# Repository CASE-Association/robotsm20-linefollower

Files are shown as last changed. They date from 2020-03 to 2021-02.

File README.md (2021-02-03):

# Blitz V2
Project repository for the line follower **Blitz V2** to compete in Robot SM 2020. Last years robot was [Blitz V1](https://github.com/caselabbet/robotsm19-linefollower).

Below is a rendered version of **Blitz V2**.
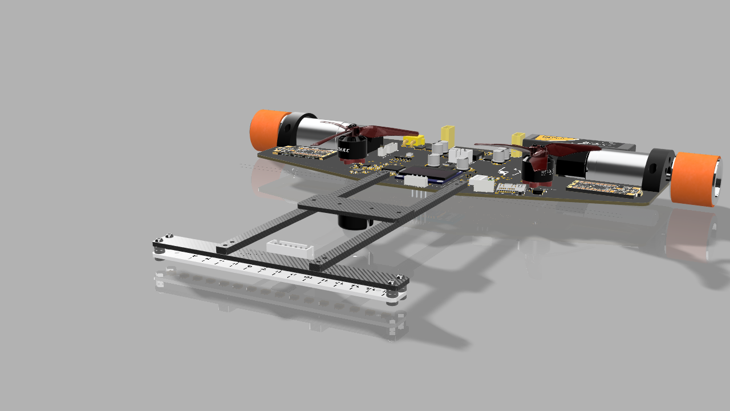
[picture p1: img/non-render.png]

## Goals 
- Utilize more advanced control algorithm.
    - Acceleration control
        - Speed trajectory planner
    - Speed control
        - PID + Anti windup + Active damping
    - Position control
        - PID + Anti windup + Active damping
    - State space model + LQG controller (*optional*)
    - MPC - Model Predictive Conrol (*optional)*
- Map race track + Path planner (*optional*)
- Beat last years result and take 1st place. (*not optional*) 
- Added hardware and improvements
    - Use of suction/exhuast fans
    - Single PCB
    - Bluetooth communication
    - High power motors (11W vs 1/2W)
 
## Directories 
```
robotsm20-linefollower
├── datasheets      
├── hardware        
│   ├── cad         # 3D models
│   │   └── stl     # 3D print files
│   └── pcb         # Schematic, layout and production files
├── img             
├── simulation      # Matlab + simulink simulations
└── software
    ├── Inc         # C header files
    └── Src         # C source files
  ```

## Development enviroment
The microcontroller configuration for peripherals such as ADC, GPIO, TIM, Clock etc. is set up via [STM32CubeMX](https://www.st.com/en/development-tools/stm32cubemx.html) (GUI) and is then ported to a PlatformIO project with the [stm32pio](https://github.com/ussserrr/stm32pio) command. The software is developed in the [VS Code](https://code.visualstudio.com/) IDE with the [PlatformIO](https://platformio.org/) plugin.

This makes it possible to generate base code for initialization of peripherals with the powerful configurator <b>STM32CubeMX</b> but also use the great </b>PlatformIO + VS code</b> ecosystem to manage compiling, uploading, debugging and scripting tasks.

## Installation
In order to update configuration in <b>STM32CubeMX</b> and then update <b>PlatformIO</b> project you need to set up your development enviroment:
 - Create a `boards` directory in your platformio home folder:
    - Unix: `~/.platformio/`
    - Windows: `%HOMEPATH%\.platformio`
 - Copy the custom board `stm32f405rg.json` to the newly created `boards` directory.
 - Verify that the board has been added by running `platformio boards stm32` and find the stm32f405 board.
    <details>
    <summary><b>Common problems</b></summary>

    - If it is not in the list, make sure you put the `boards` in the correct folder and spelled it right.

    - [platformio is not recognized as an internal command](https://docs.platformio.org/en/latest/installation.html#install-shell-commands) 
    </details>
- Rename the file `stm32pio_template.ini` inside the `software` folder to `stm32pio.ini`and fill it out according to the template:
 ```` ini
[app]
java_cmd = java
platformio_cmd = platformio
cubemx_cmd = path/to/cubemx_program

[project]
cubemx_script_content = config load path/to/cubemx_file.ioc
	generate code path/to/projectFolder
	exit
platformio_ini_patch_content = [platformio]
	include_dir = Inc
	src_dir = Src
ioc_file = path/to/cubemxfile.ioc
board = stm32f405rg
````

<details><summary>Unix example</summary>

``` ini
[app]
java_cmd = java
platformio_cmd = platformio
cubemx_cmd = /Applications/STMicroelectronics/STM32CubeMX.app/Contents/Resources/STM32CubeMX

[project]
cubemx_script_content = config load /Users/isakaslund/Documents/code/robotsm20-linefollower/software/software.ioc
	generate code /Users/isakaslund/Documents/code/robotsm20-linefollower/software/
	exit
platformio_ini_patch_content = [platformio]
	include_dir = Inc
	src_dir = Src
ioc_file = /Users/isakaslund/Documents/code/robotsm20-linefollower/software/software.ioc
board = stm32f405rg

```
</details>
<details><summary>Windows example</summary>

``` ini
[app]
java_cmd = java
platformio_cmd = platformio
cubemx_cmd = C:/Program Files/STMicroelectronics/STM32Cube/STM32CubeMX/STM32CubeMX.exe

[project]
cubemx_script_content = config load C:\Users\Isak\Documents\GitHub\robotsm20-linefollower\software\software.ioc
	generate code C:\Users\Isak\Documents\GitHub\robotsm20-linefollower
	exit
platformio_ini_patch_content = [platformio]
	include_dir = Inc
	src_dir = Src
	
ioc_file = C:\Users\Isak\Documents\GitHub\robotsm20-linefollower\software\software.ioc
board = stm32f405rg

```

</details>

Your `software` folder should look this when finished
```
software
├── Inc
│   ├── header_files.h
│   ├── ...
├── Src
│   ├── c_files.c
│   ├── ...
├── platformio.ini
├── software.ioc
├── stm32f405rg.json
└── stm32pio.ini
```

## Usage
#### Configuration change
Change configuration of peripherals in the STM32CubeMX file `software.ioc` and then save project. **DO NOT** click the `generate code` button. 

To then update the `platformio` project run the following command inside the `software` folder:
``` sh
$ stm32pio generate
```

#### Building
Use the platform build task or press the "✓" button in the bottom left in VS code

#### Uploading
A programmer called [ST-Link](https://docs.platformio.org/en/latest/plus/debug-tools/stlink.html) is needed to upload by connecting it to the SWD pins found on the robot.

Use the platform io upload task or press the "⇨" button in the bottom left in vs code. 

#### Debugging
With the STM32 processesor you can do more then `Serial.println()` debugging over serial.
You can step debug, inspect/change variables, set breakpoints and more by using the dedicated debugger/programmer `ST-Link` and the [platformio unified debugger](https://docs.platformio.org/en/latest/plus/debugging.html).

When setup you can start debugging by going to `Debug` -> `Start debugging` in the menu bar. 

## Contributors
  - Isak Åslund - aslundisak@gmail.com
  - Oskar Johansson - oskaj@student.chalmers.se

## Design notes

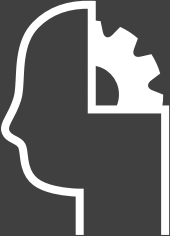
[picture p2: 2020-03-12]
hardware/pcb/decals/case_head.png

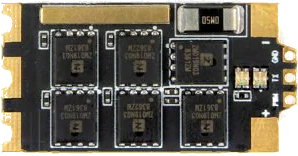
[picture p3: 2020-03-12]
hardware/pcb/decals/ESC_top.png

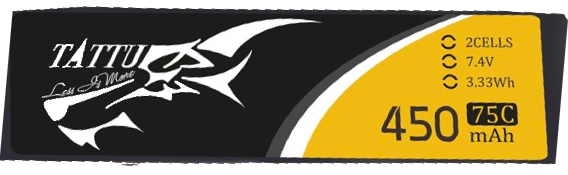
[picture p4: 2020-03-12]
hardware/pcb/decals/Tatt_2s_450mAh.png

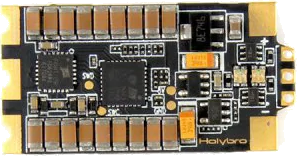
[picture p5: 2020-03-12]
hardware/pcb/decals/ESC_bottom.png

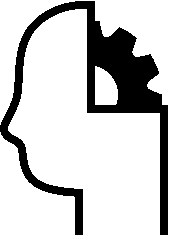
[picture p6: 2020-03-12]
hardware/pcb/case.bmp

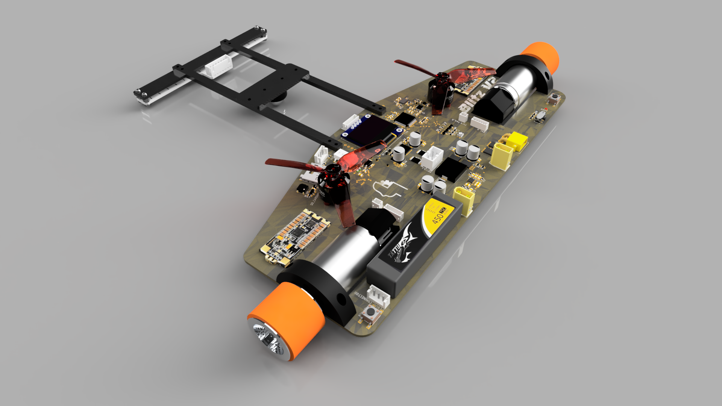
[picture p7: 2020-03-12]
img/side.png

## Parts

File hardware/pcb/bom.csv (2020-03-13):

Qty | Value | Device | Package | Parts | Description | DATASHEET-URL | DESCRIPTION | MANUFACTURER_PART_NUMBER | MOUSER_PART_NUMBER
1 |  | C-EUC0603 | C0603 | C47 | CAPACITOR, European symbol
1 |  | LEDCHIPLED_0603 | CHIPLED_0603 | LED2 | LED
1 |  | MICRO_SD_WE_693071010811 | 6,93071E+11 | SD_CARDHOLDER | WR-CRD Micro SD Card Connector Push & Push 8 pins | https://www.we-online.com/catalog/datasheet/693071010811.pdf |  | 6,93071E+11
8 | 0.1u | C-EUC0603 | C0603 | C31, C32, C34, C35, C37, C39, C40, C46 | CAPACITOR, European symbol
2 | 0.1µF | C-EUC0603 | C0603 | C3, CVCC | CAPACITOR, European symbol
4 | 0.1µF | C-EUC0805 | C0805 | C6, C7, C13, C18 | CAPACITOR, European symbol
1 | 0.68µH | SRP1238A-XXXX | INDM135125X330N | U$3 | Inductor
2 | 0R | R-EU_R0603 | R0603 | R38, R40 | RESISTOR, European symbol
1 | 1.5nF | C-EUC0805 | C0805 | C19 | CAPACITOR, European symbol
1 | 100 | R-EU_R0603 | R0603 | R37 | RESISTOR, European symbol
2 | 100R | R-EU_R0603 | R0603 | R3, R4 | RESISTOR, European symbol
2 | 100nF | C-EUC0603 | C0603 | C42, C43 | CAPACITOR, European symbol
1 | 100nF | C-EUC0805 | C0805 | C21 | CAPACITOR, European symbol
1 | 100pF | C-EUC0805 | C0805 | C26 | CAPACITOR, European symbol
6 | 100uF | WCAP-ASLL-WEWCAP-ASLL | CAPAE660X700N | C4, C15, C24, C25, C29, C30
1 | 105k | R-EU_R0603 | R0603 | R5 | RESISTOR, European symbol
2 | 10R | R-EU_R0603 | R0603 | R14, R15 | RESISTOR, European symbol
23 | 10k | R-EU_R0603 | R0603 | R1, R2, R7, R8, R11, R13, R16, R17, R18, R21, R23, R26, R27, R30, R31, R35, R39, R41, R42, R44, R45, R47, R48 | RESISTOR, European symbol
1 | 110pF | C-EUC0805 | C0805 | C20 | CAPACITOR, European symbol
1 | 120nF | C-EUC0603 | C0603 | C44 | CAPACITOR, European symbol
1 | 15.4k | R-EU_R0603 | R0603 | R10 | RESISTOR, European symbol
1 | 150141M173100 | 150141M173100 | 150141M173100 | LED1 | Wurth Elektronik 150141M173100 Common Anode RGB LED
1 | 19.4k | R-EU_R0603 | R0603 | R22 | RESISTOR, European symbol
1 | 1u | C-EUC0603 | C0603 | C33 | CAPACITOR, European symbol
2 | 2.2u | C-EUC0603 | C0603 | C36, C38 | CAPACITOR, European symbol
2 | 20k | R-EU_R0603 | R0603 | R6, R43 | RESISTOR, European symbol
4 | 22µF | C-EUC0603 | C0603 | C8, C11, C12, C17 | CAPACITOR, European symbol
5 | 22µF | C-EUC0805 | C0805 | C9, C22, C23, C27, C28 | CAPACITOR, European symbol
1 | 270pF | C-EUC0603 | C0603 | COSC | CAPACITOR, European symbol
1 | 3.14k | R-EU_R0603 | R0603 | ROSC | RESISTOR, European symbol
1 | 300R | R-EU_R0603 | R0603 | R32 | RESISTOR, European symbol
1 | 300pF | C-EUC0603 | C0603 | C16 | CAPACITOR, European symbol
1 | 3300pF | C-EUC0805 | C0805 | C10 | CAPACITOR, European symbol
2 | 4.7nF | C-EUC0603 | C0603 | C1, C2 | CAPACITOR, European symbol
1 | 4.7µF | C-EUC0805 | C0805 | C14 | CAPACITOR, European symbol
1 | 50R | R-EU_R0603 | R0603 | R36 | RESISTOR, European symbol
1 | 6.8nF | C-EUC0603 | C0603 | C45 | CAPACITOR, European symbol
1 | 62k | R-EU_R0603 | R0603 | R46 | RESISTOR, European symbol
1 | 75k | R-EU_R0603 | R0603 | R9 | RESISTOR, European symbol
1 | 88k | R-EU_R0603 | R0603 | R12 | RESISTOR, European symbol
1 | BNO055 | BNO055 | BNO055 | IMU-BNO055 | IMUs - Inertial Measurement Units Absolute Orientation 9-Axis Sensor |  | IMUs - Inertial Measurement Units Absolute Orientation 9-Axis Sensor | BNO055 | 262-BNO055
4 | BSS138LT3G | BSS138LT3G | SOT23 | Q5, Q6, Q7, Q8 | BSS138LT3G N-Channel Mosfet (SOT-23)
4 | CSD17301Q5A | CSD17301Q5A | Q5A | U$2, U$8, U$9, U$10 | CSD17301Q5A
1 | CTS_219-4LPST | CTS_219-4LPST | DIPSWITCH_4P_SMD | SW1 | 219-4LPST - Standard 4 position DIP-Switch - SMD
1 | DIODE_1N4148WX | DIODE_1N4148WX | 1N4148WX_SOD-323-2 | U$5
1 | DISPLAY-OLED-128X64-I2C | DISPLAY-OLED-128X64-I2C | DISPLAY-OLED-128X64-I2C | OLED_DISPLAY | OLED 128x63 - I2C - 0.96";";";";";";";";";";";";";";";";";"; 1" | INA2181 | INA2181
1 | JS202011AQN | JS202011AQN | JS202011AQN | BATT_SWITCH | JS202011AQN
2 | JST-EH-03 | EH_B3B-EH | B3B-EH | DEBUG_CONNECTOR, UART_CONNECTOR | JST EH Connector, through hole, 3 pin, top entry
1 | LM1117-3.3 | LM1117-3.3 | SOT230P700X180-4 | LDO_3V3 | LM1117
1 | MCP1501T-XXE | MCP1501T-XXE | SON50P200X200X80-9T80X120N | LDO_VREF_1V8 | MCP1501T-XXE
2 | R001 | R-EU_R2512W | R2512W | MOTOR_LR, MOTOR_RR | RESISTOR, European symbol
1 | R002 | R-EU_R2512W | R2512W | RSENSE | RESISTOR, European symbol
1 | SMT-0540-S-R | SMT-0540-S-R | SMT-0540-S-R | U$1 | Magnetic buzzer
2 | SPLITTER | SPLITTER | SPLITTER | U$4, U$6 | Used for separating grounds
1 | STM32F405RG | STM32F405RG | LQFP-64 | U1 | STM32F405RG Microcontroller
1 | TB67H420FTG | TB67H420FTG | QFN50P700X700X100-49T550N | MOTORDRIVER | TB67H420FTG
2 | TEST-POINT3X5 | TEST-POINT3X5 | PAD.03X.05 | TP_LO1, TP_LO2 | Test Points
4 | TEST_POINTPAD_HOLE | TEST_POINTPAD_HOLE | PAD_HOLE | TP_1V8, TP_3V3, TP_5V, TP_12V
1 | TPS43061RTER | TPS43061RTER | QFN50P300X300X80-17N | BOOST | Low Iq, Synchronous Boost Controller with Wide Input Voltage and 5.5V Gate Drive for Low Qg NexFETs |  | Low Iq, Synchronous Boost Controller with Wide Input Voltage and 5.5V Gate Drive for Low Qg NexFETs | TPS43061RTER | 595-TPS43061RTER
1 | TPS82130SILT | TPS82130SILT | TPS82130SILT | BUCK | 3-A 17V Step-down Converter Module with Integrated Inductor |  | 3-A 17V Step-down Converter Module with Integrated Inductor | TPS82130SILT | 595-TPS82130SILT
2 | TSM2JSMA | TSM2JSMA | TSM2JSMA | BTN_RESET, BTN_SEL | FSM2JSMA Tactile SPST switches
1 | WIRELESS-BLUETOOTH-HC-05 | WIRELESS-BLUETOOTH-HC-05 | WIRELESS-BLUETOOTH-HC-05 | BT_HC05 | Bluetooth Transceiver Module based on HC-05 board
2 | XH-02 | XH-02 | JST-XH-02 | MOTOR_L, MOTOR_R | JST EX Connector, through hole, 2 pin, top entry
2 | XT30 | XT30 | XT30 | FAN_POWER_L, FAN_POWER_R | XT60 Connector
1 | XT30PW-M | XT30PW-M | XT30PW-M | U$15
2 | ZH | ZR_B2B-ZR | B2B-ZR | PWM_FAN_L, PWM_FAN_R | JST ZR Connector, through hole, 2 pin, top entry
1 | ZH | ZR_B7B-ZR | B7B-ZR | XLINE | JST ZR Connector, through hole, 7 pin, top entry
2 | ZH-6 | ZR_B6B-ZR | B6B-ZR | ENC_L, ENC_R | JST ZR Connector, through hole, 6 pin, top entry

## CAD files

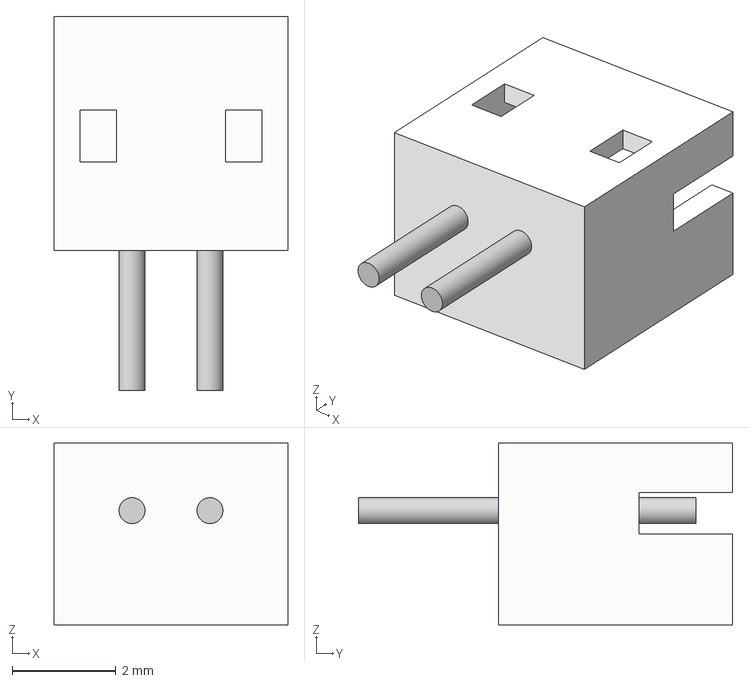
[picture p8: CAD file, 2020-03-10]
hardware/pcb/step/JST-ZH-02.step
4.50 x 7.20 x 3.50 mm

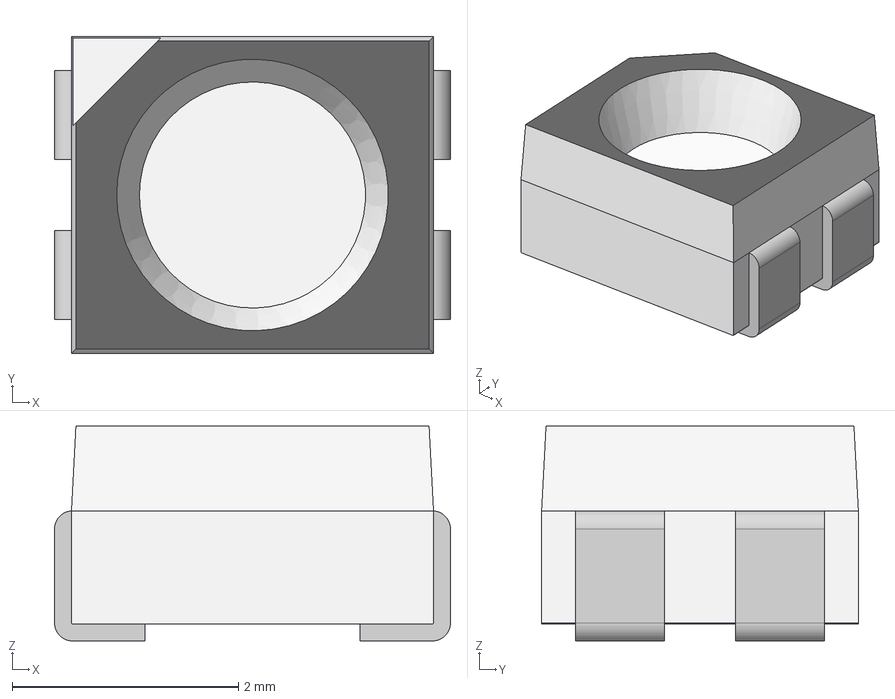
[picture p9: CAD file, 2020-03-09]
hardware/pcb/step/RGB-LED_15014M173100.step
3.50 x 2.80 x 1.90 mm
base x 2
base (1) x 2
cover
housing

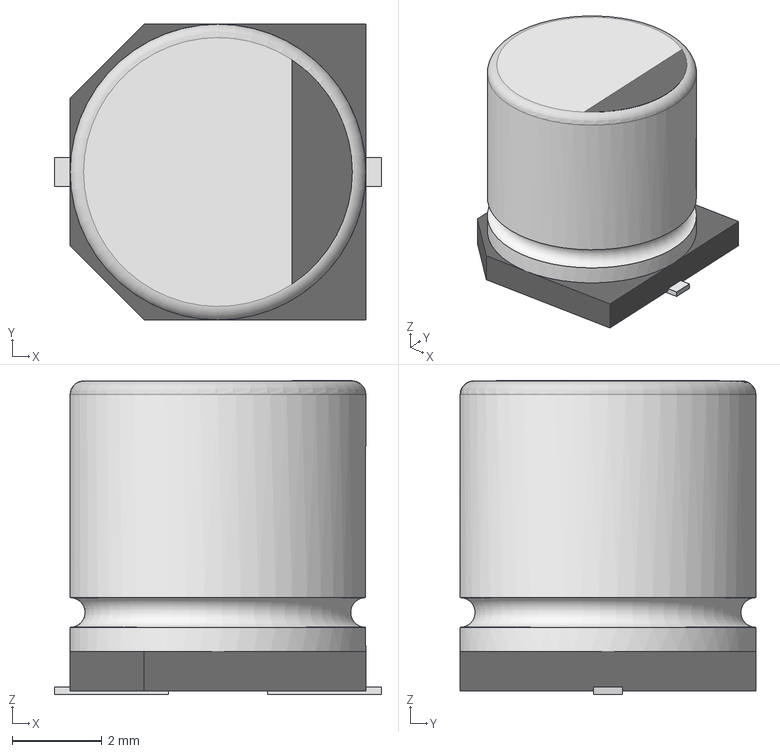
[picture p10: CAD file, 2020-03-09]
hardware/pcb/step/WCAP-ASLL.step
7.30 x 6.60 x 7.01 mm

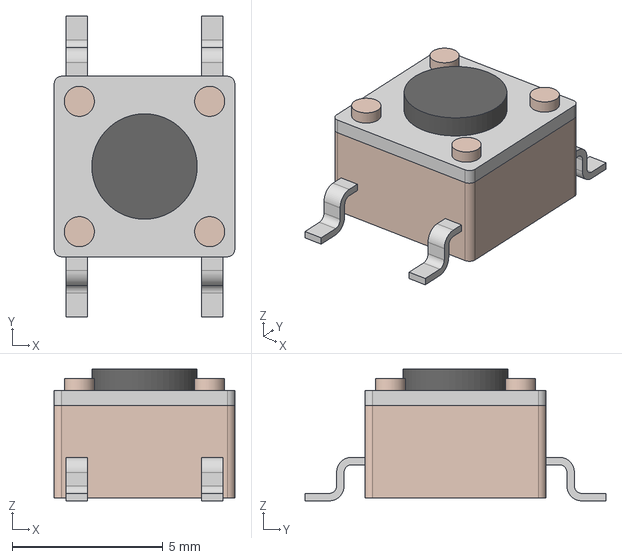
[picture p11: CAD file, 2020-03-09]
hardware/pcb/step/FSM2JSMA.step
6.00 x 10.0 x 4.38 mm

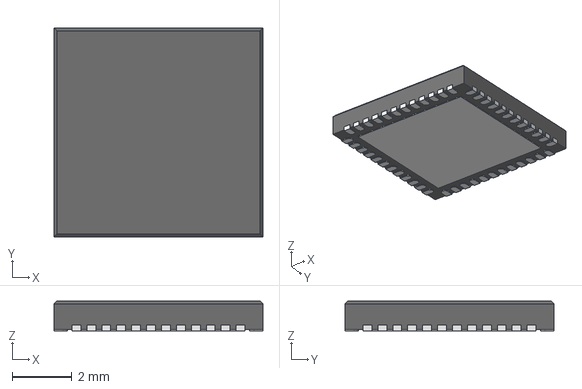
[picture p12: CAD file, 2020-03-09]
hardware/pcb/step/TB67H420_QFN48.step
7.00 x 7.00 x 1.00 mm

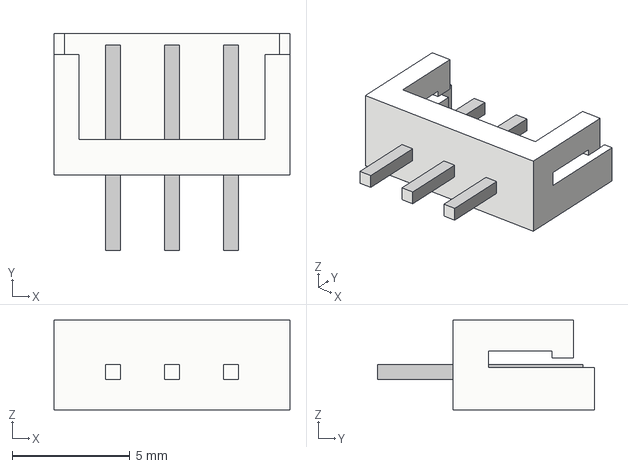
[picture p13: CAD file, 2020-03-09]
hardware/pcb/step/JST-EH-03.step
10.0 x 9.20 x 3.80 mm

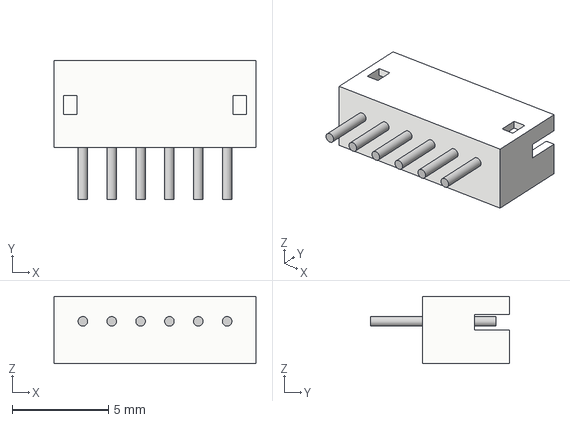
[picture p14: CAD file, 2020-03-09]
hardware/pcb/step/JST-ZH-06.step
10.5 x 7.20 x 3.50 mm

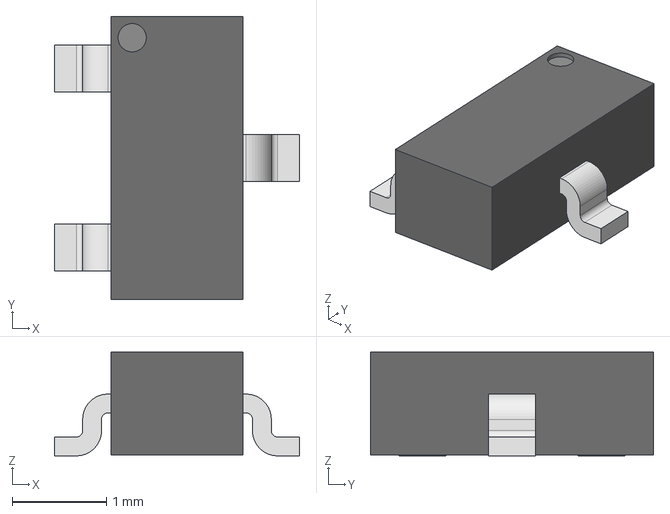
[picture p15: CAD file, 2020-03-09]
hardware/pcb/step/BSS138L.step
2.60 x 3.00 x 1.10 mm

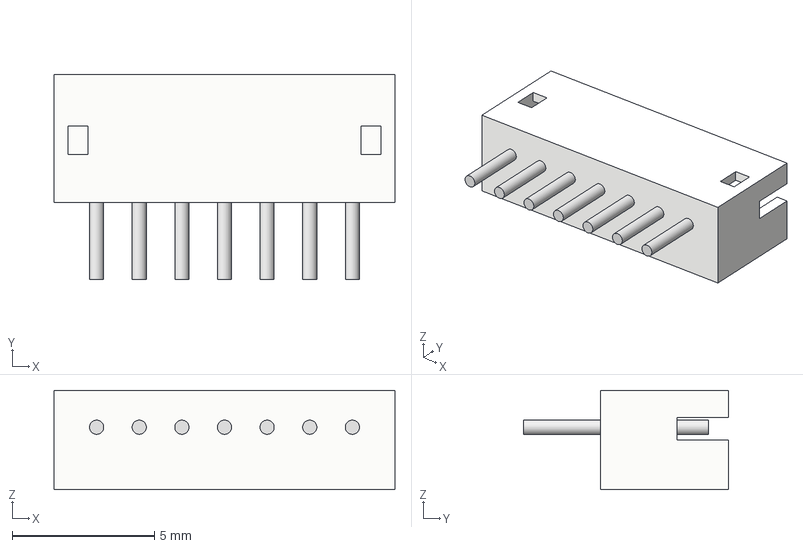
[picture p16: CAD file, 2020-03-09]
hardware/pcb/step/JST-ZH-07.step
12.0 x 7.20 x 3.50 mm

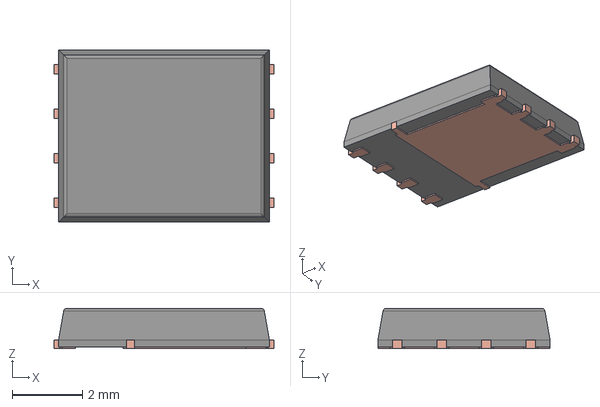
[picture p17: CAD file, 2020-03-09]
hardware/pcb/step/DQJ0008A.stp
6.26 x 4.90 x 1.15 mm
FRAME
MOLD

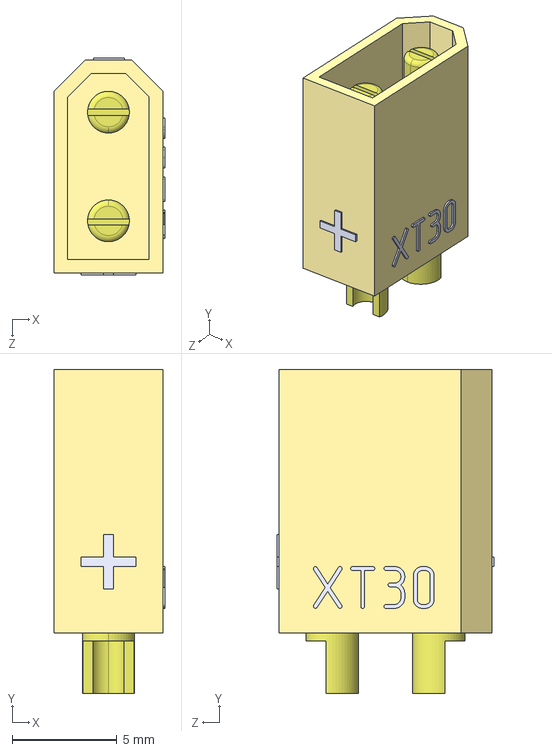
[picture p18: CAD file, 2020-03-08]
hardware/pcb/step/XT30-M.step
5.30 x 15.5 x 10.4 mm

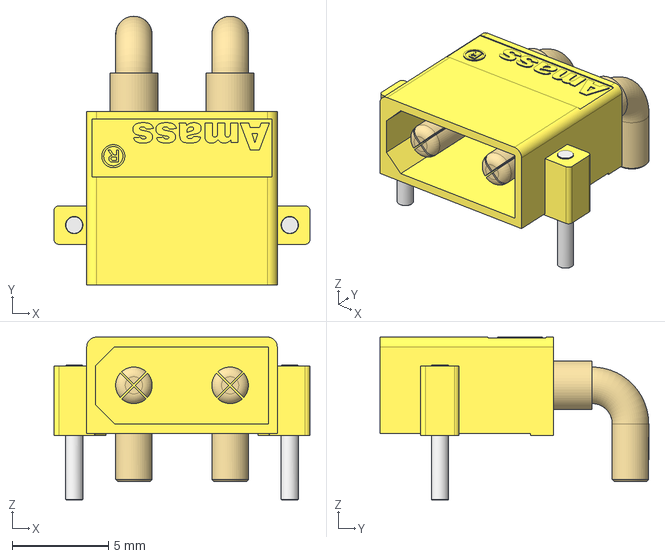
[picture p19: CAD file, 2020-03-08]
hardware/pcb/step/Amass_XT30PW-M_pcb solder.stp
13.3 x 13.9 x 8.45 mm

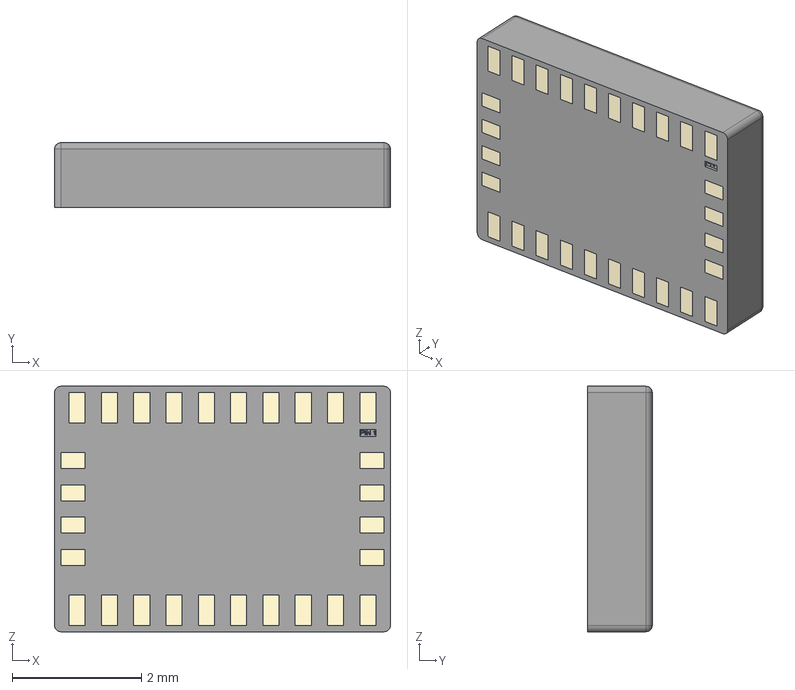
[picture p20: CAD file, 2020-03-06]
hardware/pcb/step/BNO055.step
5.20 x 1.00 x 3.80 mm

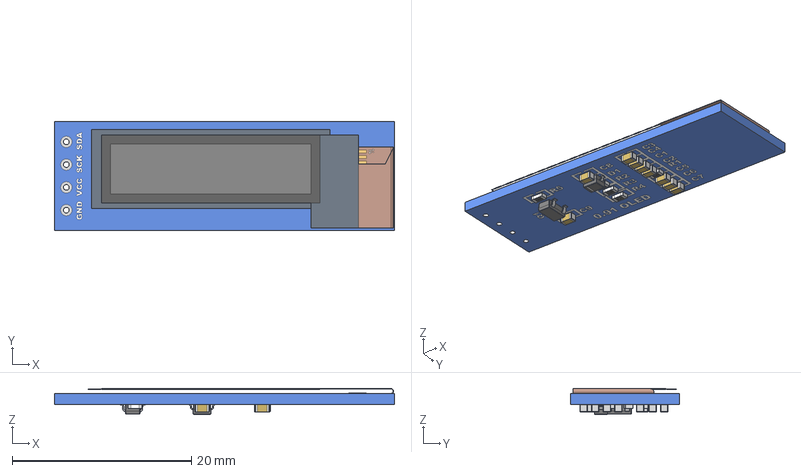
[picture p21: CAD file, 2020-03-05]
hardware/pcb/step/128x32 Oled i2c.stp
37.9 x 12.1 x 2.93 mm
0.91in oled Module - Board
0.91in OLED - Folded Flush - Without Glass
0603 Capacitor x 9
0603 Resistor x 5
SOT23-3
Diode (SOD-323)

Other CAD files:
hardware/pcb/step/JS202011AQN.step
hardware/pcb/step/TPS82130.step
hardware/pcb/step/TPS43061.step

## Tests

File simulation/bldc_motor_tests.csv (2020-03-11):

 | RS1306 + 3blade(black) |  |  | RS1306 + 3blade(red-translucent)
RPM | I | Thrust | RPM | I | Thrust
n/a | n/a | n/a | 8300 | 0,6 | 18,5
Props did not work well when reversed due to extreme shape |  |  | 14000 | 1,8 | 47,8
 |  |  | 18500 | 3,75 | 90
 |  |  | 23000 | 6,5 | 130
 | RS1606 + 3"3B(red-solid) |  |  | RS1606 + 3"4B(black-solid) |  |  | RS1606 + 4"3B(red-solid)
RPM | I | Thrust | RPM | I | Thrust | RPM | I | Thrust
8000 | 0,8 | 6 | 8800 | 1,1 | 18 | 5000 | 0,7 | 16
14000 | 1,9 | 30 | 17000 | 4 | 75 | 7700 | 1,7 | 37
20000 | 3,5 | 70 | 22000 | 7,6 | 124 | 10000 | 3,3 | 68
23000 | 4,5 | 92 |  |  |  | 12000 | 5,3 | 94
24500 | 5 | 110 |  |  |  | 13300 | 7,3 | 115
 | RS2205 + 4"4B(red-solid)
RPM | I | Thrust
5000 | 0,9 | 32
8500 | 2,8 | 90
10000 | 4,35 | 150
11300 | 6,2 | 220
12300 | 7,5 | 275

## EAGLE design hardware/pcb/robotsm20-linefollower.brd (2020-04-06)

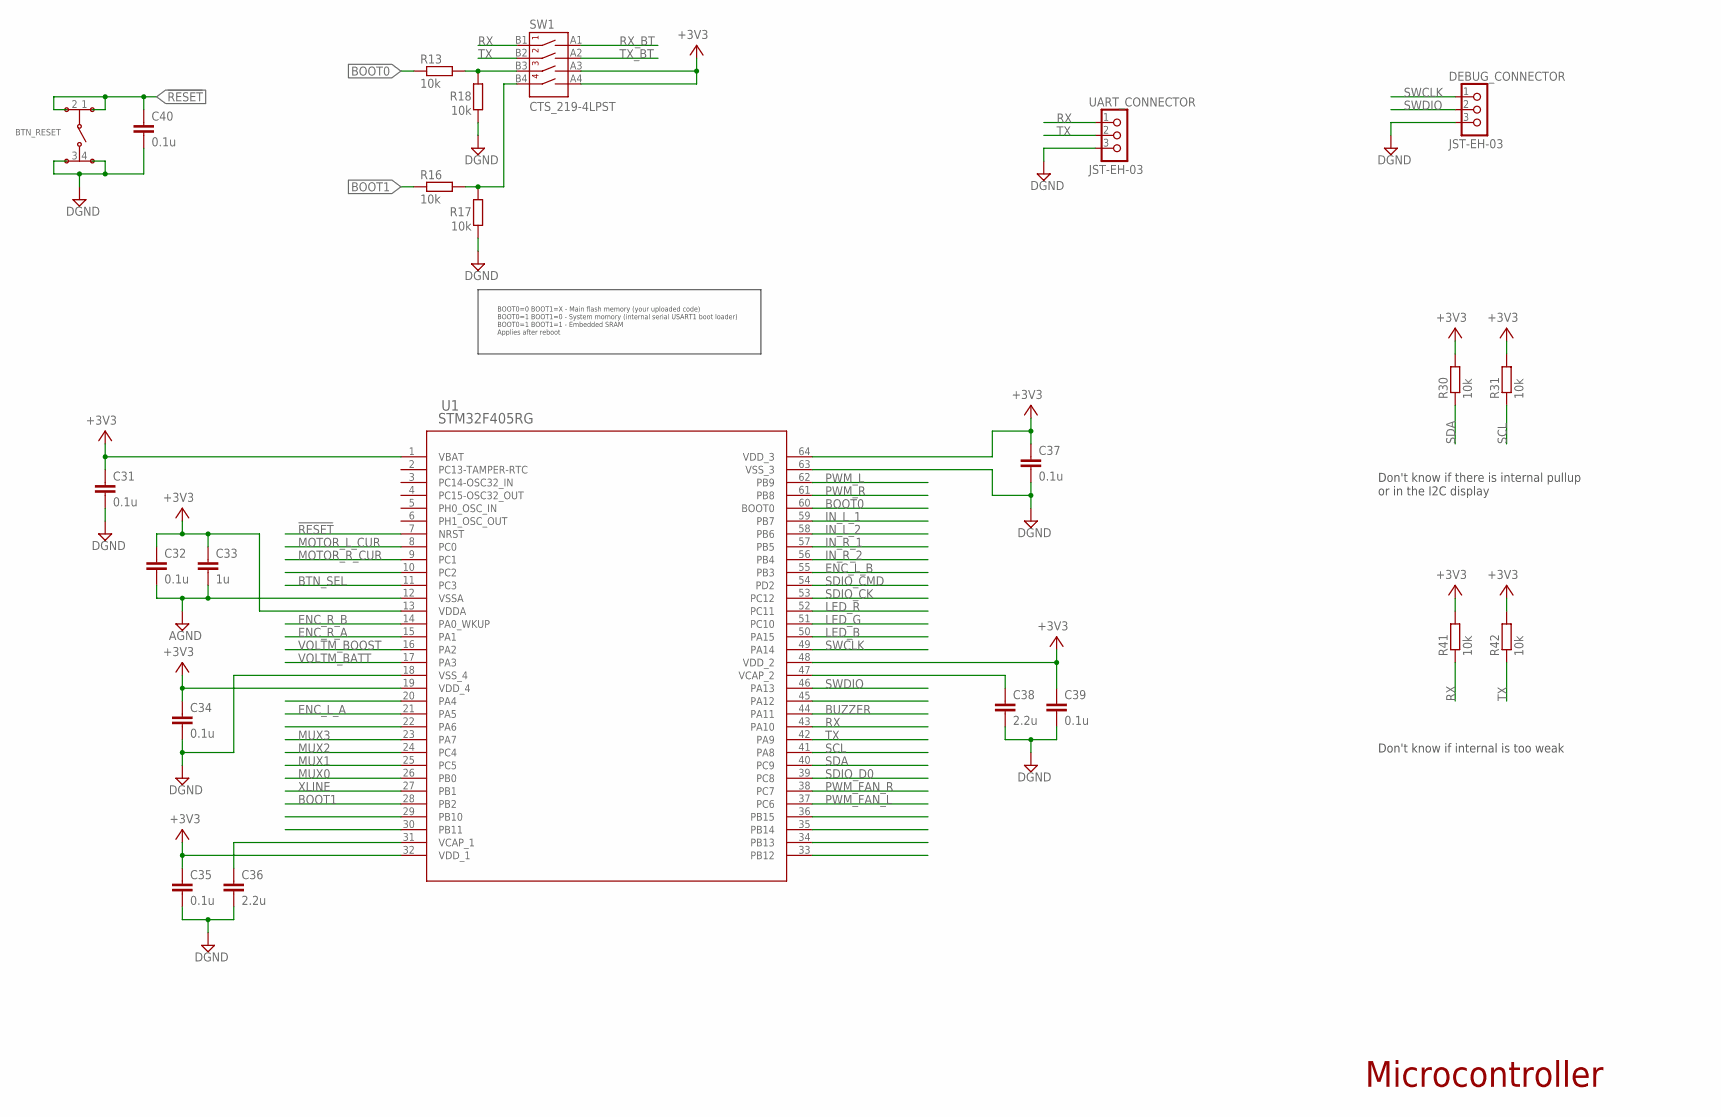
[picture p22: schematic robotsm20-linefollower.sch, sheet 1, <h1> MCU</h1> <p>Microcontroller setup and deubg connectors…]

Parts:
BTN_RESET: TSM2JSMA
C31, C32, C34, C35, C37, C39, C40: 0.1u; C0603
C33: 1u; C0603
C36, C38: 2.2u; C0603
DEBUG_CONNECTOR: JST-EH-03; B3B-EH
R13, R16, R17, R18, R30, R31, R41, R42: 10k; R0603
SW1: CTS_219-4LPST; DIPSWITCH_4P_SMD
U1: STM32F405RG; LQFP-64
UART_CONNECTOR: JST-EH-03; B3B-EH

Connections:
!RESET: BTN_RESET.1, BTN_RESET.2, C40.1, U1.7 (NRST)
+3V3: C31.1, C32.1, C33.1, C34.1, C35.1, C37.1, C39.1, R30.1, R31.1, R41.1, R42.1, SW1.A3, SW1.A4, U1.1 (VBAT), U1.13 (VDDA), U1.19 (VDD_4), U1.32 (VDD_1), U1.48 (VDD_2), U1.64 (VDD_3); also elsewhere on the board
AGND: C32.2, C33.2, U1.12 (VSSA); also elsewhere on the board
BOOT0: R13.2, U1.60 (BOOT0)
BOOT1: R16.1, U1.28 (PB2)
BTN_SEL: U1.11 (PC3); also elsewhere on the board
BUZZER: U1.44 (PA11); also elsewhere on the board
DGND: BTN_RESET.3, BTN_RESET.4, C31.2, C34.2, C35.2, C36.2, C37.2, C38.2, C39.2, C40.2, DEBUG_CONNECTOR.3, R17.1, R18.1, U1.18 (VSS_4), U1.63 (VSS_3), UART_CONNECTOR.3; also elsewhere on the board
ENC_L_A: U1.21 (PA5); also elsewhere on the board
ENC_L_B: U1.55 (PB3); also elsewhere on the board
ENC_R_A: U1.15 (PA1); also elsewhere on the board
ENC_R_B: U1.14 (PA0_WKUP); also elsewhere on the board
IN_L_1: U1.59 (PB7); also elsewhere on the board
IN_L_2: U1.58 (PB6); also elsewhere on the board
IN_R_1: U1.57 (PB5); also elsewhere on the board
IN_R_2: U1.56 (PB4); also elsewhere on the board
LED_B: U1.50 (PA15); also elsewhere on the board
LED_G: U1.51 (PC10); also elsewhere on the board
LED_R: U1.52 (PC11); also elsewhere on the board
MOTOR_L_CUR: U1.8 (PC0); also elsewhere on the board
MOTOR_R_CUR: U1.9 (PC1); also elsewhere on the board
MUX0: U1.26 (PB0); also elsewhere on the board
MUX1: U1.25 (PC5); also elsewhere on the board
MUX2: U1.24 (PC4); also elsewhere on the board
MUX3: U1.23 (PA7); also elsewhere on the board
unnamed: R16.2, R17.2, SW1.B4
unnamed: R13.1, R18.2, SW1.B3
unnamed: C36.1, U1.31 (VCAP_1)
unnamed: C38.1, U1.47 (VCAP_2)
PWM_FAN_L: U1.37 (PC6); also elsewhere on the board
PWM_FAN_R: U1.38 (PC7); also elsewhere on the board
PWM_L: U1.62 (PB9); also elsewhere on the board
PWM_R: U1.61 (PB8); also elsewhere on the board
RX: R41.2, SW1.B1, U1.43 (PA10), UART_CONNECTOR.1
RX_BT: SW1.A1; also elsewhere on the board
SCL: R31.2, U1.41 (PA8); also elsewhere on the board
SDA: R30.2, U1.40 (PC9); also elsewhere on the board
SDIO_CK: U1.53 (PC12); also elsewhere on the board
SDIO_CMD: U1.54 (PD2); also elsewhere on the board
SDIO_D0: U1.39 (PC8); also elsewhere on the board
SWCLK: DEBUG_CONNECTOR.1, U1.49 (PA14)
SWDIO: DEBUG_CONNECTOR.2, U1.46 (PA13)
TX: R42.2, SW1.B2, U1.42 (PA9), UART_CONNECTOR.2
TX_BT: SW1.A2; also elsewhere on the board
VOLTM_BATT: U1.17 (PA3); also elsewhere on the board
VOLTM_BOOST: U1.16 (PA2); also elsewhere on the board
XLINE: U1.27 (PB1); also elsewhere on the board

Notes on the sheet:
Microcontroller
BOOT0=0 BOOT1=X - Main flash memory (your uploaded code) BOOT0=1 BOOT1=0 - System momory (internal serial USART1 boot loader) BOOT0=1 BOOT1=1 - Embedded SRAM Applies after reboot
Don't know if there is internal pullup or in the I2C display
Don't know if internal is too weak

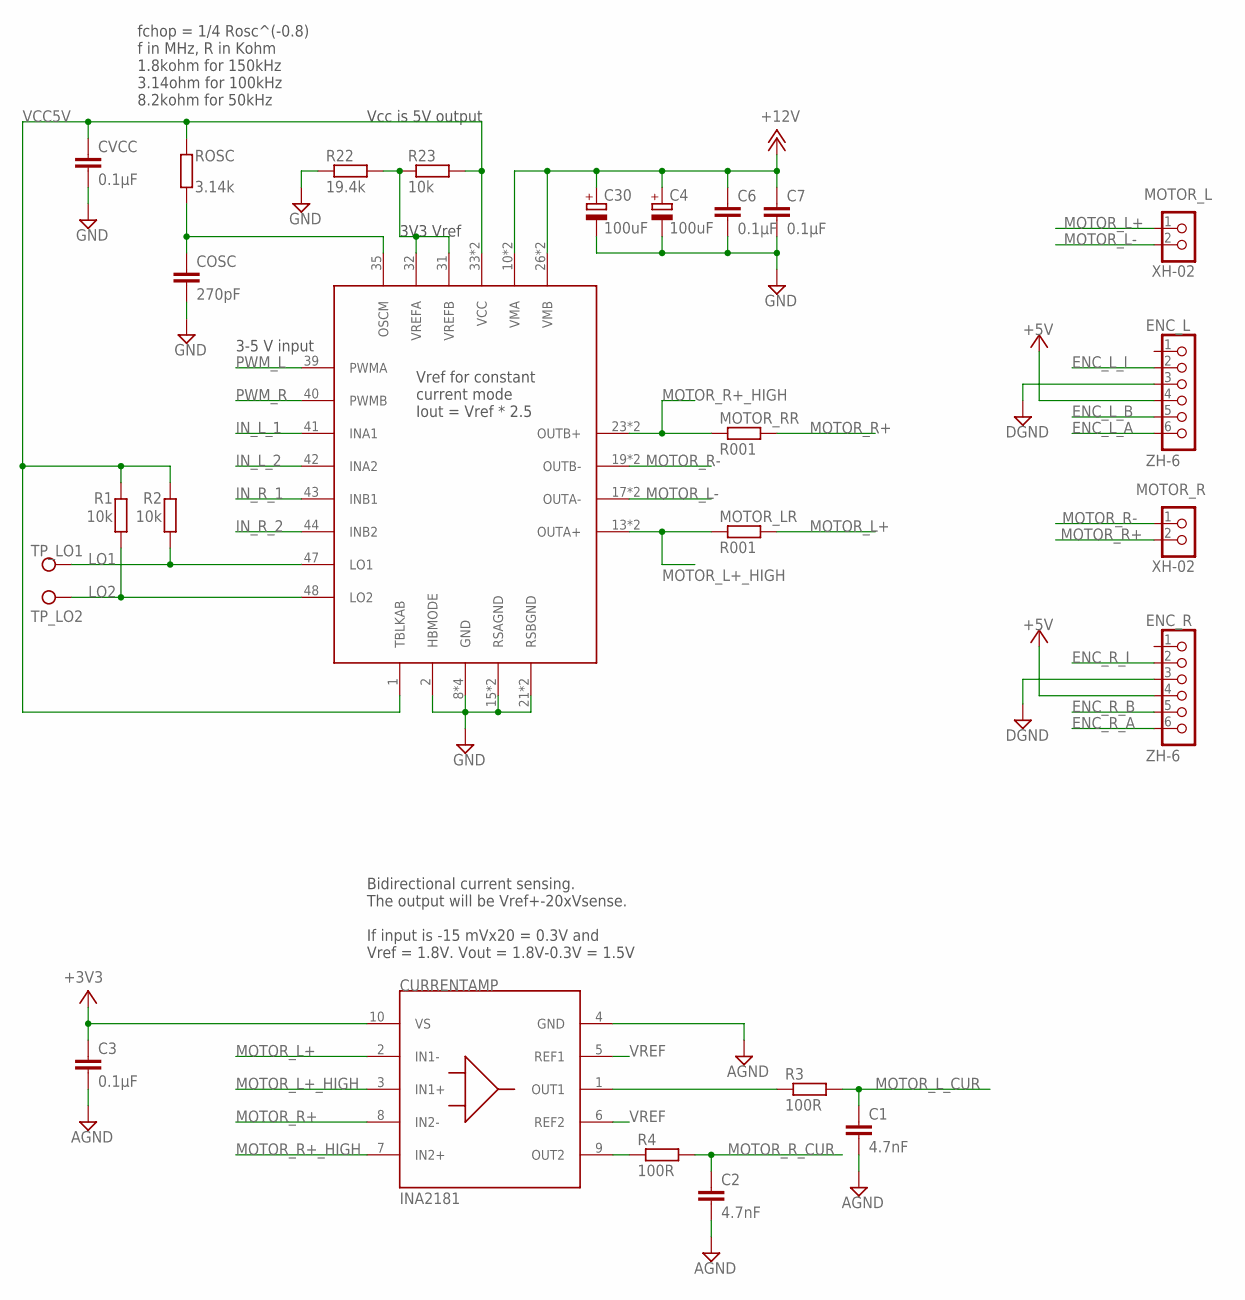
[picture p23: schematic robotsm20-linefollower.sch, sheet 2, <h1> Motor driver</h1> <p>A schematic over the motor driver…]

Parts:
C1, C2: 4.7nF; C0603
C3: 0.1µF; C0603
C4, C30: 100uF; CAPAE660X700N
C6, C7: 0.1µF; C0805
COSC: 270pF; C0603
CURRENTAMP: INA2181; SOP50P490X110-10N
CVCC: 0.1µF; C0603
ENC_L: ZH-6; B6B-ZR
ENC_R: ZH-6; B6B-ZR
MOTORDRIVER: TB67H420FTG; QFN50P700X700X100-49T550N
MOTOR_L: XH-02; JST-XH-02
MOTOR_LR: R001; R2512W
MOTOR_R: XH-02; JST-XH-02
MOTOR_RR: R001; R2512W
R1, R2, R23: 10k; R0603
R3, R4: 100R; R0603
R22: 19.4k; R0603
ROSC: 3.14k; R0603
TP_LO1, TP_LO2: TEST-POINT3X5; PAD.03X.05

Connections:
+3V3: C3.1, CURRENTAMP.10 (VS); also elsewhere on the board
+5V: ENC_L.4, ENC_R.4; also elsewhere on the board
+12V: C4.1 (+), C6.1, C7.1, C30.1 (+), MOTORDRIVER.10 (VMA), MOTORDRIVER.11 (VMA), MOTORDRIVER.26 (VMB), MOTORDRIVER.27 (VMB); also elsewhere on the board
AGND: C1.2, C2.2, C3.2, CURRENTAMP.4 (GND); also elsewhere on the board
DGND: ENC_L.3, ENC_R.3; also elsewhere on the board
ENC_L_A: ENC_L.6; also elsewhere on the board
ENC_L_B: ENC_L.5; also elsewhere on the board
ENC_L_I: ENC_L.2
ENC_R_A: ENC_R.6; also elsewhere on the board
ENC_R_B: ENC_R.5; also elsewhere on the board
ENC_R_I: ENC_R.2
GND: C4.2 (-), C6.2, C7.2, C30.2 (-), COSC.2, CVCC.2, MOTORDRIVER.2 (HBMODE), MOTORDRIVER.8 (GND), MOTORDRIVER.15 (RSAGND), MOTORDRIVER.16 (RSAGND), MOTORDRIVER.21 (RSBGND), MOTORDRIVER.22 (RSBGND), MOTORDRIVER.29 (GND), MOTORDRIVER.30 (GND), MOTORDRIVER.49 (GND), R22.1; also elsewhere on the board
IN_L_1: MOTORDRIVER.41 (INA1); also elsewhere on the board
IN_L_2: MOTORDRIVER.42 (INA2); also elsewhere on the board
IN_R_1: MOTORDRIVER.43 (INB1); also elsewhere on the board
IN_R_2: MOTORDRIVER.44 (INB2); also elsewhere on the board
LO1: MOTORDRIVER.47 (LO1), R2.1, TP_LO1.P$1
LO2: MOTORDRIVER.48 (LO2), R1.1, TP_LO2.P$1
MOTOR_L+: CURRENTAMP.2 (IN1-), MOTOR_L.1, MOTOR_LR.2
MOTOR_L+_HIGH: CURRENTAMP.3 (IN1+), MOTORDRIVER.13 (OUTA+), MOTORDRIVER.14 (OUTA+), MOTOR_LR.1
MOTOR_L-: MOTORDRIVER.17 (OUTA-), MOTORDRIVER.18 (OUTA-), MOTOR_L.2
MOTOR_L_CUR: C1.1, R3.2; also elsewhere on the board
MOTOR_R+: CURRENTAMP.8 (IN2-), MOTOR_R.2, MOTOR_RR.2
MOTOR_R+_HIGH: CURRENTAMP.7 (IN2+), MOTORDRIVER.23 (OUTB+), MOTORDRIVER.24 (OUTB+), MOTOR_RR.1
MOTOR_R-: MOTORDRIVER.19 (OUTB-), MOTORDRIVER.20 (OUTB-), MOTOR_R.1
MOTOR_R_CUR: C2.1, R4.2; also elsewhere on the board
unnamed: CURRENTAMP.9 (OUT2), R4.1
unnamed: CURRENTAMP.1 (OUT1), R3.1
unnamed: MOTORDRIVER.31 (VREFB), MOTORDRIVER.32 (VREFA), R22.2, R23.1
unnamed: COSC.1, MOTORDRIVER.35 (OSCM), ROSC.1
PWM_L: MOTORDRIVER.39 (PWMA); also elsewhere on the board
PWM_R: MOTORDRIVER.40 (PWMB); also elsewhere on the board
VCC5V: CVCC.1, MOTORDRIVER.1 (TBLKAB), MOTORDRIVER.33 (VCC), MOTORDRIVER.34 (VCC), R1.2, R2.2, R23.2, ROSC.2
VREF: CURRENTAMP.5 (REF1), CURRENTAMP.6 (REF2); also elsewhere on the board

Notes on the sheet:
Bidirectional current sensing. The output will be Vref+-20xVsense. If input is -15 mVx20 = 0.3V and Vref = 1.8V. Vout = 1.8V-0.3V = 1.5V
3-5 V input
Vcc is 5V output
3V3 Vref
fchop = 1/4 Rosc^(-0.8) f in MHz, R in Kohm 1.8kohm for 150kHz 3.14ohm for 100kHz 8.2kohm for 50kHz
Vref for constant current mode Iout = Vref * 2.5

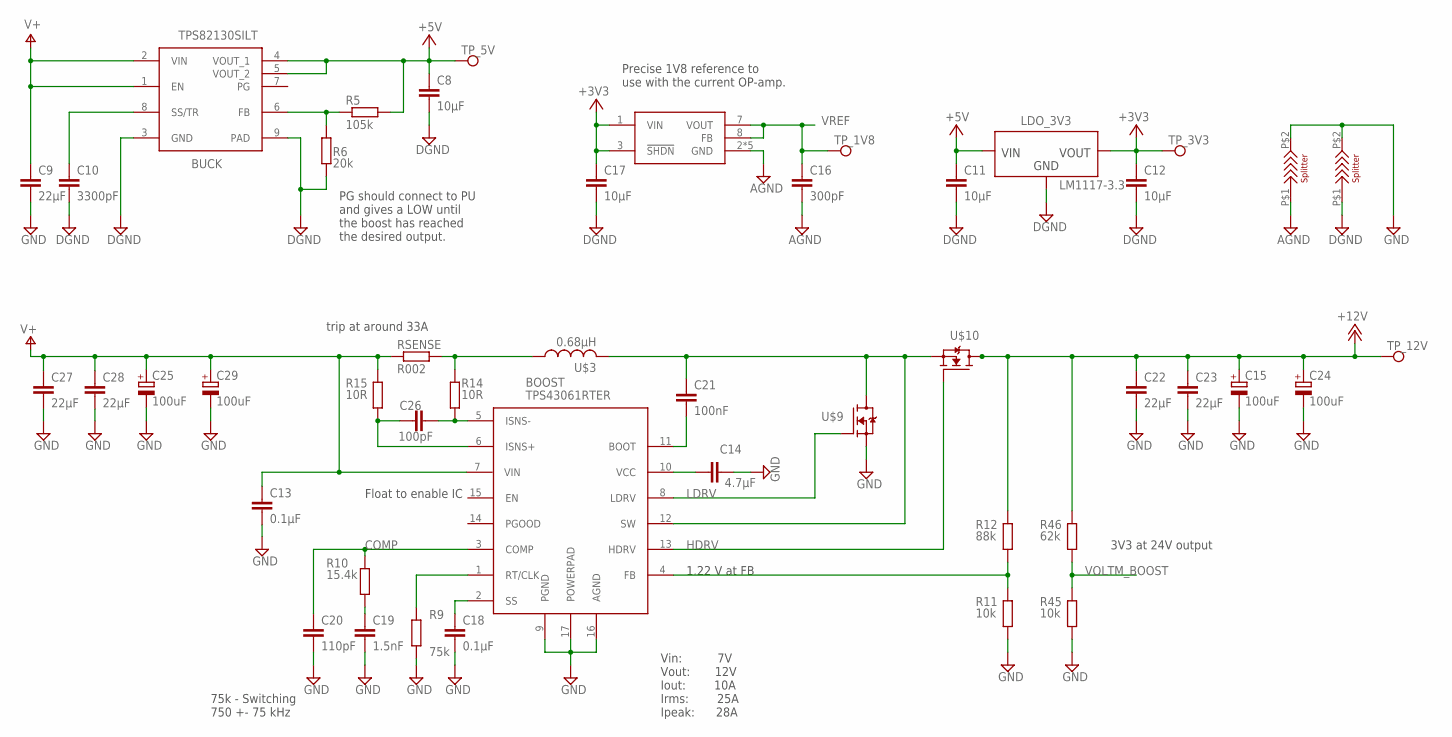
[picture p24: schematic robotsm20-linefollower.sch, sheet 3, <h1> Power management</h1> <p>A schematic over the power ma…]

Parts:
BOOST: TPS43061RTER; QFN50P300X300X80-17N
BUCK: TPS82130SILT
C8, C11, C12, C17: 10µF; C0603
C9, C22, C23, C27, C28: 22µF; C0805
C10: 3300pF; C0805
C13, C18: 0.1µF; C0805
C14: 4.7µF; C0805
C15, C24, C25, C29: 100uF; CAPAE660X700N
C16: 300pF; C0603
C19: 1.5nF; C0805
C20: 110pF; C0805
C21: 100nF; C0805
C26: 100pF; C0805
LDO_3V3: LM1117-3.3; SOT230P700X180-4
LDO_VREF_1V8: MCP1501T-XXE; SON50P200X200X80-9T80X120N
R5: 105k; R0603
R6: 20k; R0603
R9: 75k; R0603
R10: 15.4k; R0603
R11, R45: 10k; R0603
R12: 88k; R0603
R14, R15: 10R; R0603
R46: 62k; R0603
RSENSE: R002; R2512W
TP_1V8, TP_3V3, TP_5V, TP_12V: TEST_POINTPAD_HOLE; PAD_HOLE
U$3: 0.68µH; INDM135125X330N
U$4, U$6: SPLITTER
U$9, U$10: CSD17301Q5A; Q5A

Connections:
+3V3: C12.1, C17.1, LDO_3V3.2 (VOUT), LDO_3V3.4 (VOUT), LDO_VREF_1V8.1 (VIN), LDO_VREF_1V8.3 (!SHDN!), TP_3V3.P$1; also elsewhere on the board
+5V: BUCK.4 (VOUT_1), BUCK.5 (VOUT_2), C8.1, C11.1, LDO_3V3.3 (VIN), R5.2, TP_5V.P$1; also elsewhere on the board
+12V: C15.1 (+), C22.1, C23.1, C24.1 (+), R12.2, R46.2, TP_12V.P$1, U$10.5 (D), U$10.6 (D), U$10.7 (D), U$10.8 (D), U$10.9 (D); also elsewhere on the board
AGND: C16.2, LDO_VREF_1V8.2 (GND), LDO_VREF_1V8.4 (GND), LDO_VREF_1V8.5 (GND), LDO_VREF_1V8.6 (GND), LDO_VREF_1V8.9 (GND), U$4.P$1 (1); also elsewhere on the board
COMP: BOOST.3 (COMP), C20.1, R10.2
DGND: BUCK.3 (GND), BUCK.9 (PAD), C8.2, C10.2, C11.2, C12.2, C17.2, LDO_3V3.1 (GND), R6.1, U$6.P$1 (1); also elsewhere on the board
GND: BOOST.9 (PGND), BOOST.16 (AGND), BOOST.17 (POWERPAD), C9.2, C13.2, C14.2, C15.2 (-), C18.2, C19.2, C20.2, C22.2, C23.2, C24.2 (-), C25.2 (-), C27.2, C28.2, C29.2 (-), R9.1, R11.1, R45.1, U$4.P$2 (2), U$6.P$2 (2), U$9.1 (S), U$9.2 (S), U$9.3 (S); also elsewhere on the board
HDRV: BOOST.13 (HDRV), U$10.4 (G)
LDRV: BOOST.8 (LDRV), U$9.4 (G)
unnamed: BOOST.10 (VCC), C14.1
unnamed: BUCK.8 (SS/TR), C10.1
unnamed: BUCK.6 (FB), R5.1, R6.2
unnamed: BOOST.1 (RT/CLK), R9.2
unnamed: BOOST.2 (SS), C18.1
unnamed: C19.1, R10.1
unnamed: BOOST.11 (BOOT), C21.2
unnamed: R14.2, RSENSE.2, U$3.1
unnamed: BOOST.12 (SW), C21.1, U$3.2, U$9.5 (D), U$9.6 (D), U$9.7 (D), U$9.8 (D), U$9.9 (D), U$10.1 (S), U$10.2 (S), U$10.3 (S)
unnamed: BOOST.4 (FB), R11.2, R12.1
unnamed: BOOST.5 (ISNS-), C26.2, R14.1
unnamed: BOOST.6 (ISNS+), C26.1, R15.1
V+: BOOST.7 (VIN), BUCK.1 (EN), BUCK.2 (VIN), C9.1, C13.1, C25.1 (+), C27.1, C28.1, C29.1 (+), R15.2, RSENSE.1; also elsewhere on the board
VOLTM_BOOST: R45.2, R46.1; also elsewhere on the board
VREF: C16.1, LDO_VREF_1V8.7 (VOUT), LDO_VREF_1V8.8 (FB), TP_1V8.P$1; also elsewhere on the board

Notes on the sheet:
PG should connect to PU and gives a LOW until the boost has reached the desired output.
Precise 1V8 reference to use with the current OP-amp.
75k - Switching 750 +- 75 kHz
1.22 V at FB
trip at around 33A
Vin: 7V Vout: 12V Iout: 10A Irms: 25A Ipeak: 28A
3V3 at 24V output
Float to enable IC

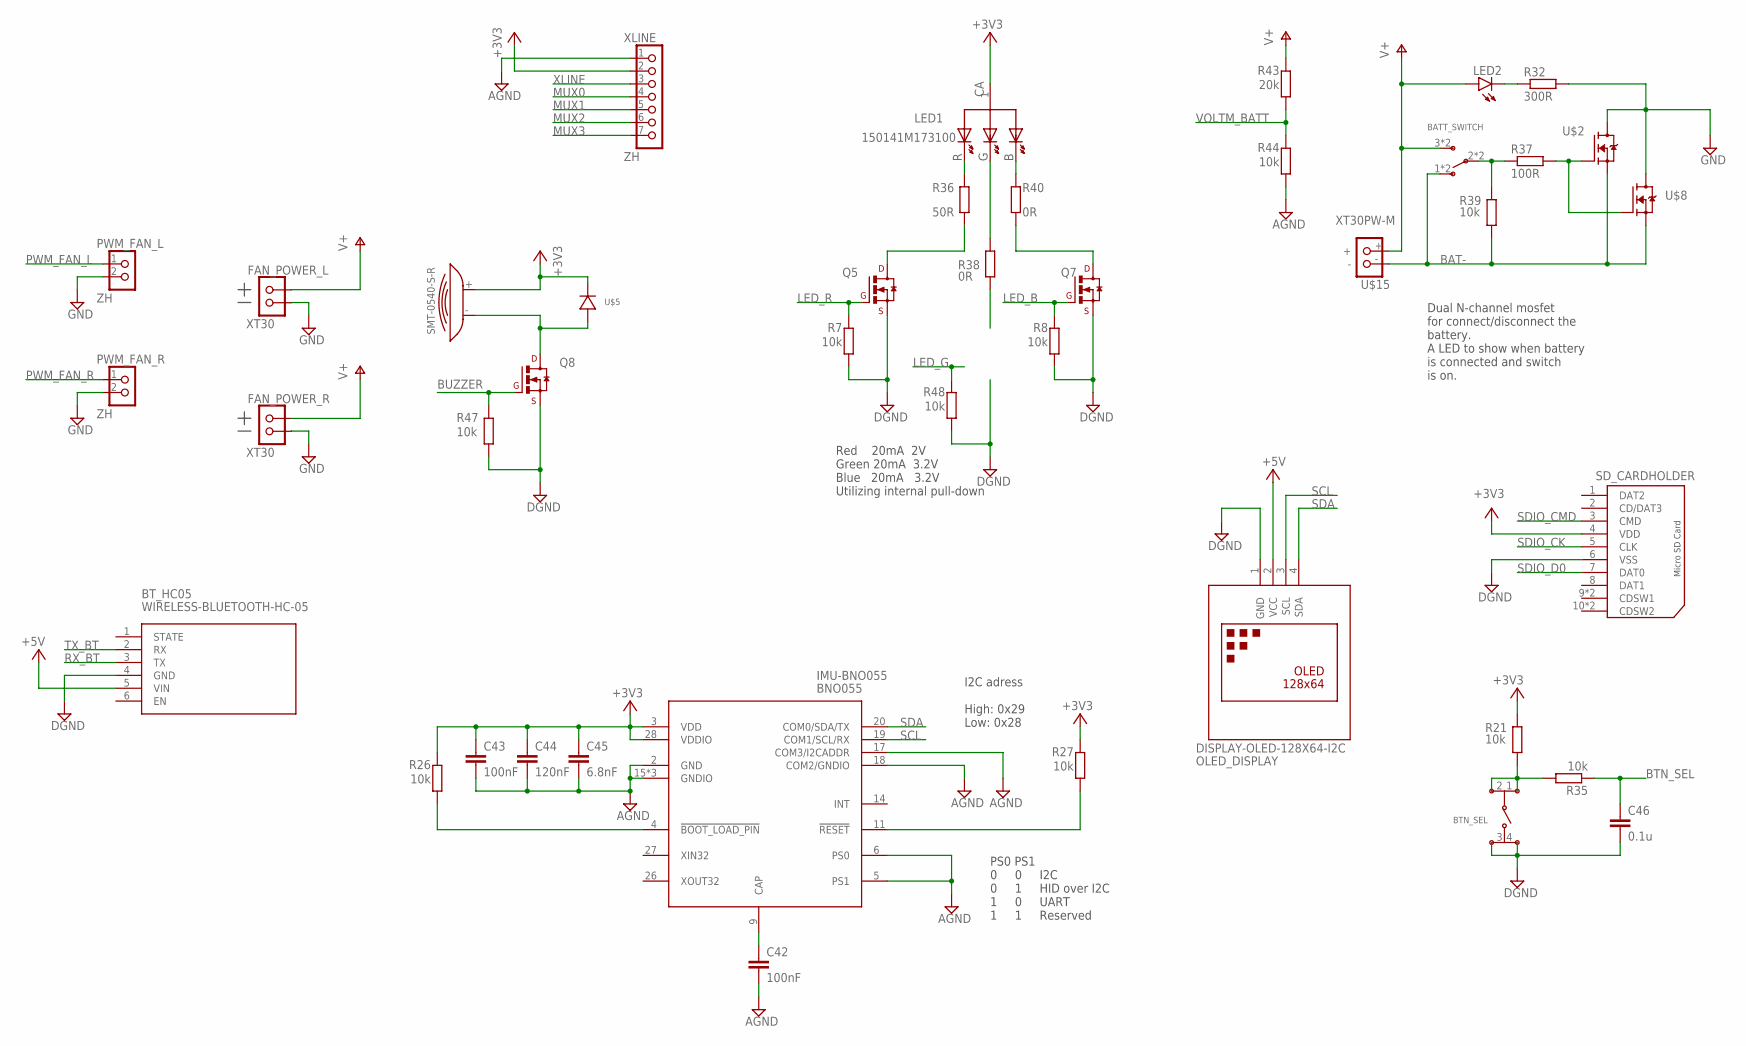
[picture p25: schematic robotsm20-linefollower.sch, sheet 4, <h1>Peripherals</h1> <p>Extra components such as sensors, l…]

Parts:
BATT_SWITCH: JS202011AQN
BTN_SEL: TSM2JSMA
BT_HC05: WIRELESS-BLUETOOTH-HC-05
C42, C43: 100nF; C0603
C44: 120nF; C0603
C45: 6.8nF; C0603
C46: 0.1u; C0603
FAN_POWER_L: XT30
FAN_POWER_R: XT30
IMU-BNO055: BNO055
LED1: 150141M173100
LED2: LEDCHIPLED_0603; CHIPLED_0603
OLED_DISPLAY: DISPLAY-OLED-128X64-I2C
PWM_FAN_L: ZH; B2B-ZR
PWM_FAN_R: ZH; B2B-ZR
Q5, Q7, Q8: BSS138LT3G; SOT23
R7, R8, R21, R26, R27, R35, R39, R44, R47, R48: 10k; R0603
R32: 300R; R0603
R36: 50R; R0603
R37: 100R; R0603
R38, R40: 0R; R0603
R43: 20k; R0603
SD_CARDHOLDER: MICRO_SD_WE_693071010811; 693071010811
U$1: SMT-0540-S-R
U$2, U$8: CSD17301Q5A; Q5A
U$5: DIODE_1N4148WX; 1N4148WX_SOD-323-2
U$15: XT30PW-M
XLINE: ZH; B7B-ZR

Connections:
+3V3: C43.1, C44.1, C45.1, IMU-BNO055.3 (VDD), IMU-BNO055.28 (VDDIO), LED1.1 (CA), R21.1, R26.2, R27.2, SD_CARDHOLDER.4 (VDD), U$1.+, U$5.- (-_CATHODE), XLINE.2; also elsewhere on the board
+5V: BT_HC05.5 (VIN), OLED_DISPLAY.2 (VCC); also elsewhere on the board
AGND: C42.2, C43.2, C44.2, C45.2, IMU-BNO055.2 (GND), IMU-BNO055.5 (PS1), IMU-BNO055.6 (PS0), IMU-BNO055.15 (GNDIO), IMU-BNO055.16 (GNDIO), IMU-BNO055.17 (COM3/I2CADDR), IMU-BNO055.18 (COM2/GNDIO), IMU-BNO055.25 (GNDIO), R44.2, XLINE.1; also elsewhere on the board
BAT-: BATT_SWITCH.1 (NC), BATT_SWITCH.4 (NC), R39.1, U$2.1 (S), U$2.2 (S), U$2.3 (S), U$8.1 (S), U$8.2 (S), U$8.3 (S), U$15.-
BTN_SEL: C46.1, R35.1; also elsewhere on the board
BUZZER: Q8.1 (G), R47.1; also elsewhere on the board
DGND: BTN_SEL.3, BTN_SEL.4, BT_HC05.4 (GND), C46.2, OLED_DISPLAY.1 (GND), Q5.2 (S), Q7.2 (S), Q8.2 (S), R7.1, R8.1, R47.2, R48.1, SD_CARDHOLDER.6 (VSS); also elsewhere on the board
GND: FAN_POWER_L.NEG-, FAN_POWER_R.NEG-, PWM_FAN_L.2, PWM_FAN_R.2, R32.1, U$2.5 (D), U$2.6 (D), U$2.7 (D), U$2.8 (D), U$2.9 (D), U$8.5 (D), U$8.6 (D), U$8.7 (D), U$8.8 (D), U$8.9 (D); also elsewhere on the board
LED_B: Q7.1 (G), R8.2; also elsewhere on the board
LED_G: R48.2; also elsewhere on the board
LED_R: Q5.1 (G), R7.2; also elsewhere on the board
MUX0: XLINE.4; also elsewhere on the board
MUX1: XLINE.5; also elsewhere on the board
MUX2: XLINE.6; also elsewhere on the board
MUX3: XLINE.7; also elsewhere on the board
unnamed: BTN_SEL.1, BTN_SEL.2, R21.2, R35.2
unnamed: IMU-BNO055.11 (!RESET!), R27.1
unnamed: C42.1, IMU-BNO055.9 (CAP)
unnamed: Q8.3 (D), U$1.-, U$5.+ (+_ANODE)
unnamed: IMU-BNO055.4 (!BOOT_LOAD_PIN!), R26.1
unnamed: LED2.C, R32.2
unnamed: LED1.3 (R), R36.2
unnamed: R37.1, U$2.4 (G), U$8.4 (G)
unnamed: LED1.4 (G), R38.2
unnamed: LED1.2 (B), R40.2
unnamed: Q5.3 (D), R36.1
unnamed: BATT_SWITCH.2 (COM), BATT_SWITCH.5 (COM), R37.2, R39.2
unnamed: Q7.3 (D), R40.1
PWM_FAN_L: PWM_FAN_L.1; also elsewhere on the board
PWM_FAN_R: PWM_FAN_R.1; also elsewhere on the board
RX_BT: BT_HC05.3 (TX); also elsewhere on the board
SCL: IMU-BNO055.19 (COM1/SCL/RX), OLED_DISPLAY.3 (SCL); also elsewhere on the board
SDA: IMU-BNO055.20 (COM0/SDA/TX), OLED_DISPLAY.4 (SDA); also elsewhere on the board
SDIO_CK: SD_CARDHOLDER.5 (CLK); also elsewhere on the board
SDIO_CMD: SD_CARDHOLDER.3 (CMD); also elsewhere on the board
SDIO_D0: SD_CARDHOLDER.7 (DAT0); also elsewhere on the board
TX_BT: BT_HC05.2 (RX); also elsewhere on the board
V+: BATT_SWITCH.3 (NO), BATT_SWITCH.6 (NO), FAN_POWER_L.POS+, FAN_POWER_R.POS+, LED2.A, R43.1, U$15.+; also elsewhere on the board
VOLTM_BATT: R43.2, R44.1; also elsewhere on the board
XLINE: XLINE.3; also elsewhere on the board

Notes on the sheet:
I2C adress High: 0x29 Low: 0x28
Dual N-channel mosfet for connect/disconnect the battery. A LED to show when battery is connected and switch is on.
Red 20mA 2V Green 20mA 3.2V Blue 20mA 3.2V Utilizing internal pull-down
PS0 PS1 0 0 I2C 0 1 HID over I2C 1 0 UART 1 1 Reserved

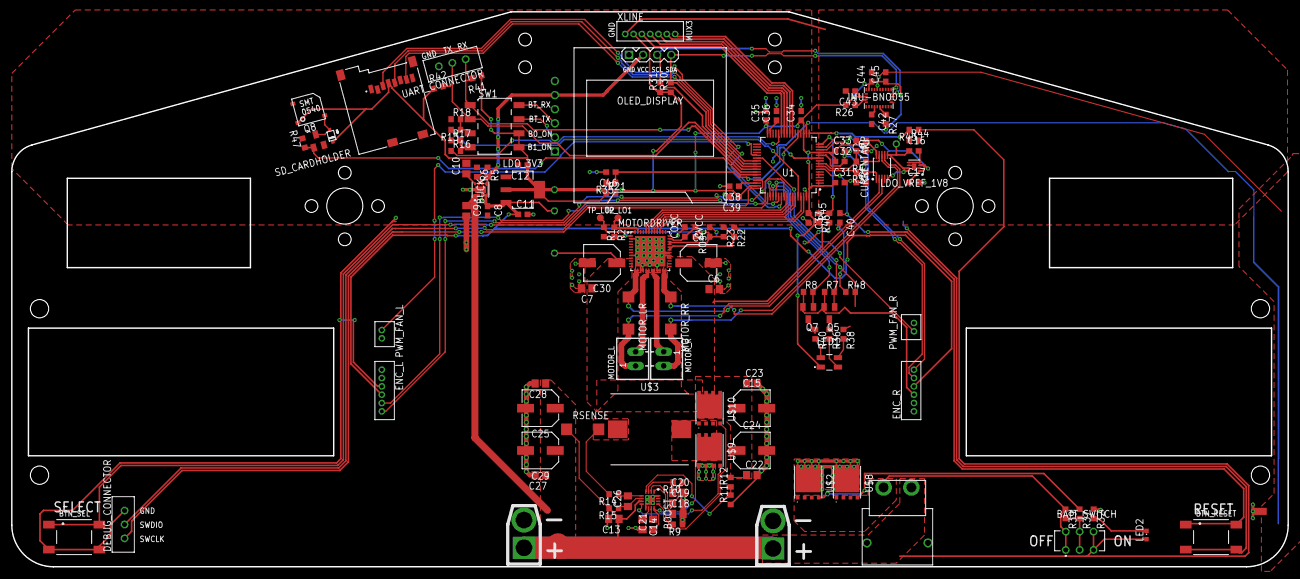
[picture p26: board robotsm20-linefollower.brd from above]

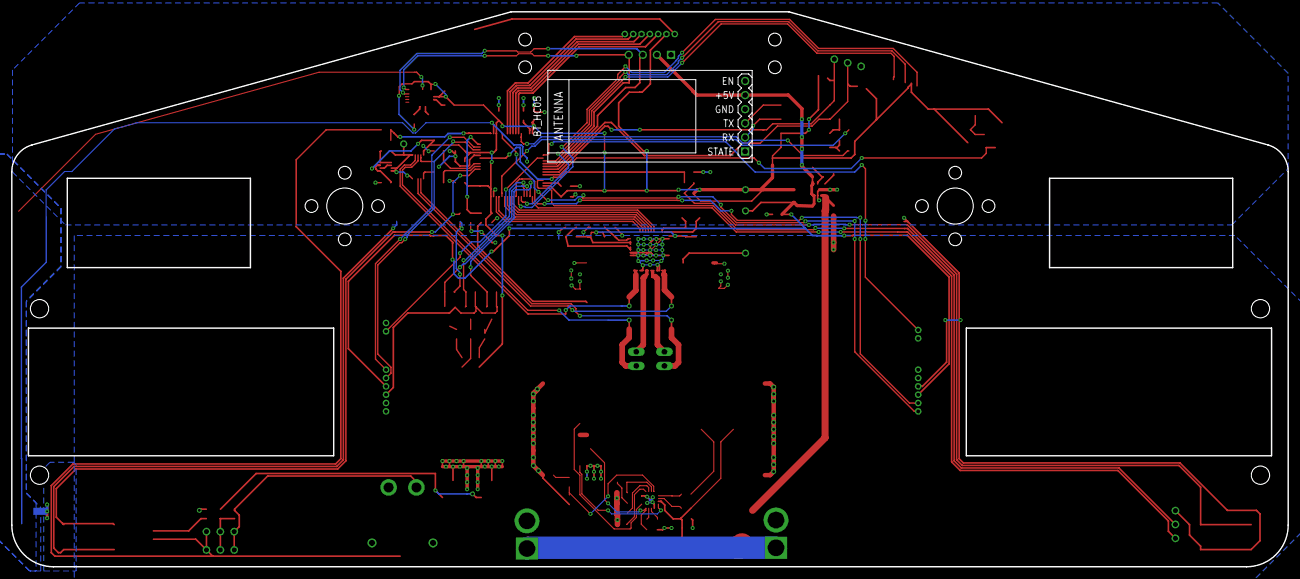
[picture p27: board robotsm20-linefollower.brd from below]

Board: 2 copper layers, 230.0 x 100.0 mm, 137 parts (2 on the bottom side), 94 nets.

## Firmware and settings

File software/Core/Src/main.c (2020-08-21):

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

/* Includes ------------------------------------------------------------------*/
#include "main.h"

/* USER CODE BEGIN Includes */
#include <stdio.h>
#include <string.h>
//#include "eeprom.h"
#include <user/voltmeter.h>
#include "user/buzzer.h"
#include "user/oled.h"
#include "user/motor.h"
#include "user/fan.h"
#include "user/xline.h"
#include "user/control.h"

/* USER CODE END Includes */

ADC_HandleTypeDef hadc1;
ADC_HandleTypeDef hadc2;
DMA_HandleTypeDef hdma_adc1;

I2C_HandleTypeDef hi2c3;

TIM_HandleTypeDef htim1;
TIM_HandleTypeDef htim2;
TIM_HandleTypeDef htim3;
TIM_HandleTypeDef htim4;
TIM_HandleTypeDef htim5;
TIM_HandleTypeDef htim14;

UART_HandleTypeDef huart1;

// EEPROM memory
// The addresses that are assigned to a specific variable. It is predefined and cannot be changed.
/*uint16_t VirtAddVarTab[NB_OF_VAR] = {0X1110, 0x1111, 0x1112, 0x1113, 0x1114, 0x1115, 0x1116, 0x1117, 0x1118, 0x1119, 0x111A, 0x111B, 0x111C, 0x111D, 0x111E, 0x111F,
									 0x1120, 0x1121, 0x1122, 0x1123, 0x1124, 0x1125, 0x1126, 0x1127, 0x1128, 0x1129, 0x112A, 0x112B, 0x112C, 0x112D, 0x112E, 0x112F,
									 0X1130, 0x1131, 0x1132, 0x1133, 0x1134, 0x1135, 0x1136, 0x1137, 0x1138, 0x1139, 0x113A, 0x113B, 0x113C, 0x113D, 0x113E, 0x113F,
									 0x1140, 0x1141, 0x1142, 0x1143, 0x1144, 0x1145, 0x1146, 0x1147, 0x1148, 0x1149, 0x114A, 0x114B, 0x114C, 0x114D, 0x114E, 0x114F};
uint16_t VarDataTab[NB_OF_VAR] = {0, 0, 0, 0, 0, 0, 0, 0, 0, 0, 0, 0, 0, 0, 0, 0, 0, 0, 0, 0, 0, 0, 0, 0, 0, 0, 0, 0, 0, 0, 0, 0,
								  0, 0, 0, 0, 0, 0, 0, 0, 0, 0, 0, 0, 0, 0, 0, 0, 0, 0, 0, 0, 0, 0, 0, 0, 0, 0, 0, 0, 0, 0, 0, 0};
uint16_t VarValue = 0;
*/
void SystemClock_Config(void);
static void MX_GPIO_Init(void);
static void MX_DMA_Init(void);
static void MX_I2C3_Init(void);
static void MX_TIM1_Init(void);
static void MX_USART1_UART_Init(void);
static void MX_TIM4_Init(void);
static void MX_TIM3_Init(void);
static void MX_ADC1_Init(void);
static void MX_TIM2_Init(void);
static void MX_TIM5_Init(void);
static void MX_TIM14_Init(void);
static void MX_ADC2_Init(void);
/* USER CODE BEGIN PFP */
#ifdef __GNUC__
	#define PUTCHAR_PROTOTYPE int __io_putchar(int ch)
#else
	#define PUTCHAR_PROTOTYPE int fputc(int ch, FILE *f)
#endif
PUTCHAR_PROTOTYPE{
	HAL_UART_Transmit(&huart1, (uint8_t *) &ch, 1, 0xFFFF);
	return ch;
}

void tests_run(){
	HAL_GPIO_WritePin(LED_R_GPIO_Port, LED_R_Pin, GPIO_PIN_RESET);
	HAL_GPIO_WritePin(LED_G_GPIO_Port, LED_G_Pin, GPIO_PIN_RESET);
	HAL_GPIO_WritePin(LED_B_GPIO_Port, LED_B_Pin, GPIO_PIN_RESET);
	printf("\r\n========== RUN TESTS ==========\r\n");
	printf("\t- Buzzer\r\n");
	test_buzzer();
	HAL_Delay(2000);
	printf("\t- Motors\r\n");
	test_motors();
	HAL_Delay(2000);
	printf("\t- Fans\r\n");
	test_fan();
	HAL_Delay(2000);
}

/* USER CODE END PFP */

/* USER CODE BEGIN 0 */

// Test variables during development



/* USER CODE END 0 */

/**
  * @brief  The application entry point.
  * @retval int
  */
int main(void)
{
  /* MCU Configuration--------------------------------------------------------*/

  /* Reset of all peripherals, Initializes the Flash interface and the Systick. */
  HAL_Init();

  /* Configure the system clock */
  SystemClock_Config();

  /* Initialize all configured peripherals */
  MX_GPIO_Init();
  MX_DMA_Init();
  MX_I2C3_Init();
  MX_TIM1_Init();
  MX_USART1_UART_Init();
  MX_TIM4_Init();
  MX_TIM3_Init();
  MX_ADC1_Init();
  MX_TIM2_Init();
  MX_TIM5_Init();
  MX_TIM14_Init();
  MX_ADC2_Init();
  /* USER CODE BEGIN 2 */
  printf("========== Blitz V2 ==========\r\n");
  printf("Created by Oskar & Isak\r\n");


  printf("\r\n========== Initializing peripherals ==========\r\n");
  printf("\t- Buzzer\r\n");
  init_buzzer();
  //Startup beep
  HAL_GPIO_TogglePin(LED_R_GPIO_Port, LED_R_Pin);
	tone(523,200);
	HAL_GPIO_TogglePin(LED_R_GPIO_Port, LED_R_Pin);

	HAL_GPIO_TogglePin(LED_G_GPIO_Port, LED_G_Pin);
	tone(659,200);
	HAL_GPIO_TogglePin(LED_G_GPIO_Port, LED_G_Pin);

	HAL_GPIO_TogglePin(LED_B_GPIO_Port, LED_B_Pin);
	tone(784,200);
	HAL_GPIO_TogglePin(LED_B_GPIO_Port, LED_B_Pin);
	HAL_Delay(500);

  printf("\t- OLED\r\n");
  init_oled(); // Draws CASE LOGO for now
  //HAL_Delay(500);
  printf("\t- Motors\r\n");
  init_motors();
  //HAL_Delay(500);
  printf("\t- Fans\r\n");
  init_fans();
 // HAL_Delay(3000); //Wait for fans to beep
  printf("\t- Voltage meter\r\n");
  init_voltmeter();
  printf("\t- XLINE\r\n");
	init_xline();



  // Run all tests
  //tests_run();


  printf("\r\n========== Starting Blitz ==========\r\n");

  /* USER CODE END 2 */

  /* Infinite loop */
  /* USER CODE BEGIN WHILE */
  while (1)
  {
    /* USER CODE END WHILE */

    /* USER CODE BEGIN 3 */
  	oled_update();
  	HAL_GPIO_TogglePin(LED_B_GPIO_Port, LED_B_Pin);
  	HAL_Delay(10);

  	control_loop();
  }
  /* USER CODE END 3 */
}

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


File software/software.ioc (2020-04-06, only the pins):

Mcu.UserName=STM32F405RGTx
PA0-WKUP.GPIO_Label=ENC_R_B
PA0-WKUP.Signal=S_TIM5_CH1
PA1.GPIO_Label=ENC_R_A
PA1.Signal=S_TIM5_CH2
PA10.GPIO_Label=RX
PA10.Signal=USART1_RX
PA11.GPIO_Label=BUZZER
PA11.Signal=S_TIM1_CH4
PA13.GPIO_Label=SWDIO
PA13.Signal=SYS_JTMS-SWDIO
PA14.GPIO_Label=SWCLK
PA14.Signal=SYS_JTCK-SWCLK
PA15.GPIO_Label=LED_B
PA15.Signal=GPIO_Output
PA2.GPIO_Label=VOLTM_BOOST
PA2.Signal=ADCx_IN2
PA3.GPIO_Label=VOLTM_BATT
PA3.Signal=ADCx_IN3
PA5.GPIO_Label=ENC_L_A
PA5.Signal=S_TIM2_CH1_ETR
PA7.GPIO_Label=MUX3
PA7.Signal=GPIO_Output
PA8.GPIO_Label=SCL
PA8.Signal=I2C3_SCL
PA9.GPIO_Label=TX
PA9.Signal=USART1_TX
PB0.GPIO_Label=MUX0
PB0.Signal=GPIO_Output
PB1.GPIO_Label=XLINE
PB1.Signal=ADCx_IN9
PB2.GPIO_Label=BOOT1
PB2.Signal=GPIO_Output
PB3.GPIO_Label=ENC_L_B
PB3.Signal=S_TIM2_CH2
PB4.GPIO_Label=MOTOR_R_IN2
PB4.Signal=GPIO_Output
PB5.GPIO_Label=MOTOR_R_IN1
PB5.Signal=GPIO_Output
PB6.GPIO_Label=MOTOR_L_IN2
PB6.Signal=GPIO_Output
PB7.GPIO_Label=MOTOR_L_IN1
PB7.Signal=GPIO_Output
PB8.GPIO_Label=MOTOR_R_PWM
PB8.Signal=S_TIM4_CH3
PB9.GPIO_Label=MOTOR_L_PWM
PB9.Signal=S_TIM4_CH4
PC0.GPIO_Label=MOTOR_L_CURR
PC0.Signal=ADCx_IN10
PC1.GPIO_Label=MOTOR_R_CURR
PC1.Signal=ADCx_IN11
PC10.GPIO_Label=LED_G
PC10.Signal=GPIO_Output
PC11.GPIO_Label=LED_R
PC11.Signal=GPIO_Output
PC3.GPIO_Label=BUTTON_SELECT
PC3.Signal=GPXTI3
PC4.GPIO_Label=MUX2
PC4.Signal=GPIO_Output
PC5.GPIO_Label=MUX1
PC5.Signal=GPIO_Output
PC6.GPIO_Label=FAN_L_PWM
PC6.Signal=S_TIM3_CH1
PC7.GPIO_Label=FAN_R_PWM
PC7.Signal=S_TIM3_CH2
PC9.GPIO_Label=SDA
PC9.Signal=I2C3_SDA

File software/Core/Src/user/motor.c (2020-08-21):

#include "user/motor.h"
#include "main.h"

extern TIM_HandleTypeDef htim2;
extern TIM_HandleTypeDef htim4;
extern TIM_HandleTypeDef htim5;

void init_motors(void){
    // Start encoder inputs
    HAL_TIM_Encoder_Start(&htim5, TIM_CHANNEL_ALL); // Right
    HAL_TIM_Encoder_Start(&htim2, TIM_CHANNEL_ALL); // Left

    // Start PWM generation for motors
    HAL_TIM_PWM_Start(&htim4, TIM_CHANNEL_3); // Right
    HAL_TIM_PWM_Start(&htim4, TIM_CHANNEL_4); // Left


    motors_stop();
}

int limit_speed(int speed){
	// Max is 1000
	int max_speed = 150;
    if(speed > max_speed){
        speed = max_speed;
    }else if(speed < -max_speed){
        speed = -max_speed;
    }
    return speed;
}


void motor_l_set_speed(int speed){
    int limited_speed = limit_speed(speed);

    if(limited_speed < 0){
        limited_speed = -limited_speed;
        HAL_GPIO_WritePin(MOTOR_L_IN1_GPIO_Port, MOTOR_L_IN1_Pin, GPIO_PIN_RESET);
				HAL_GPIO_WritePin(MOTOR_L_IN2_GPIO_Port, MOTOR_L_IN2_Pin, GPIO_PIN_SET);
    }else{
        HAL_GPIO_WritePin(MOTOR_L_IN1_GPIO_Port, MOTOR_L_IN1_Pin, GPIO_PIN_SET);
				HAL_GPIO_WritePin(MOTOR_L_IN2_GPIO_Port, MOTOR_L_IN2_Pin, GPIO_PIN_RESET);
    }

    TIM4->CCR4 = limited_speed;
}

void motor_r_set_speed(int speed){
    int limited_speed = limit_speed(speed);

    if(limited_speed < 0){
        limited_speed = -limited_speed;
        HAL_GPIO_WritePin(MOTOR_R_IN1_GPIO_Port, MOTOR_R_IN1_Pin, GPIO_PIN_RESET);
        HAL_GPIO_WritePin(MOTOR_R_IN2_GPIO_Port, MOTOR_R_IN2_Pin, GPIO_PIN_SET);
        
    }else{   
        HAL_GPIO_WritePin(MOTOR_R_IN1_GPIO_Port, MOTOR_R_IN1_Pin, GPIO_PIN_SET);
        HAL_GPIO_WritePin(MOTOR_R_IN2_GPIO_Port, MOTOR_R_IN2_Pin, GPIO_PIN_RESET);
    }

    TIM4->CCR3 = limited_speed;
}

void motors_stop(void){
		// Put both motors in Hi-Z (high impedance output => rotate freely)

    TIM4->CCR3 = 0;
    HAL_GPIO_WritePin(MOTOR_R_IN1_GPIO_Port, MOTOR_R_IN1_Pin, GPIO_PIN_RESET);
    HAL_GPIO_WritePin(MOTOR_R_IN2_GPIO_Port, MOTOR_R_IN2_Pin, GPIO_PIN_RESET);

    TIM4->CCR4 = 0;
    HAL_GPIO_WritePin(MOTOR_L_IN1_GPIO_Port, MOTOR_L_IN1_Pin, GPIO_PIN_RESET);
    HAL_GPIO_WritePin(MOTOR_L_IN2_GPIO_Port, MOTOR_L_IN2_Pin, GPIO_PIN_RESET);
};


/**
 * Test motors by spinning them and showing directions with LED. Forward = green, Backwards = red
 * 1. Left forward, wait 1s, left backwards, wait 1s.
 * 2. Right forward, wait 1s, right backwards, wait 1s.
 */
void test_motors(void){
		//Left forward
		motor_l_set_speed(100);
		HAL_GPIO_WritePin(LED_G_GPIO_Port, LED_G_Pin, GPIO_PIN_SET);
		HAL_Delay(1000);

		//Wait 1s
		motor_l_set_speed(0);
		HAL_GPIO_WritePin(LED_G_GPIO_Port, LED_G_Pin, GPIO_PIN_RESET);
		HAL_Delay(1000);

		//Left backwards
		motor_l_set_speed(-100);
		HAL_GPIO_WritePin(LED_R_GPIO_Port, LED_R_Pin, GPIO_PIN_SET);
		HAL_Delay(1000);

		//Wait 1s
		motor_l_set_speed(0);
		HAL_GPIO_WritePin(LED_R_GPIO_Port, LED_R_Pin, GPIO_PIN_RESET);
		HAL_Delay(1000);




		//Right forward
		motor_r_set_speed(100);
		HAL_GPIO_WritePin(LED_G_GPIO_Port, LED_G_Pin, GPIO_PIN_SET);
		HAL_Delay(1000);

		//Wait 1s
		motor_r_set_speed(0);
		HAL_GPIO_WritePin(LED_G_GPIO_Port, LED_G_Pin, GPIO_PIN_RESET);
		HAL_Delay(1000);

		//Right backwards
		motor_r_set_speed(-100);
		HAL_GPIO_WritePin(LED_R_GPIO_Port, LED_R_Pin, GPIO_PIN_SET);
		HAL_Delay(1000);

		//Wait 1s
		motor_r_set_speed(0);
		HAL_GPIO_WritePin(LED_R_GPIO_Port, LED_R_Pin, GPIO_PIN_RESET);
		HAL_Delay(1000);
}

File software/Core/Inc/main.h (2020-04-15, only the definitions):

#define BUTTON_SELECT_Pin GPIO_PIN_3
#define BUTTON_SELECT_GPIO_Port GPIOC
#define BUTTON_SELECT_EXTI_IRQn EXTI3_IRQn
#define ENC_R_B_Pin GPIO_PIN_0
#define ENC_R_B_GPIO_Port GPIOA
#define ENC_R_A_Pin GPIO_PIN_1
#define ENC_R_A_GPIO_Port GPIOA
#define VOLTM_BOOST_Pin GPIO_PIN_2
#define VOLTM_BOOST_GPIO_Port GPIOA
#define VOLTM_BATT_Pin GPIO_PIN_3
#define VOLTM_BATT_GPIO_Port GPIOA
#define ENC_L_A_Pin GPIO_PIN_5
#define ENC_L_A_GPIO_Port GPIOA
#define MUX3_Pin GPIO_PIN_7
#define MUX3_GPIO_Port GPIOA
#define MUX2_Pin GPIO_PIN_4
#define MUX2_GPIO_Port GPIOC
#define MUX1_Pin GPIO_PIN_5
#define MUX1_GPIO_Port GPIOC
#define MUX0_Pin GPIO_PIN_0
#define MUX0_GPIO_Port GPIOB
#define XLINE_Pin GPIO_PIN_1
#define XLINE_GPIO_Port GPIOB
#define BOOT1_Pin GPIO_PIN_2
#define BOOT1_GPIO_Port GPIOB
#define FAN_L_PWM_Pin GPIO_PIN_6
#define FAN_L_PWM_GPIO_Port GPIOC
#define FAN_R_PWM_Pin GPIO_PIN_7
#define FAN_R_PWM_GPIO_Port GPIOC
#define SDA_Pin GPIO_PIN_9
#define SDA_GPIO_Port GPIOC
#define SCL_Pin GPIO_PIN_8
#define SCL_GPIO_Port GPIOA
#define TX_Pin GPIO_PIN_9
#define TX_GPIO_Port GPIOA
#define RX_Pin GPIO_PIN_10
#define RX_GPIO_Port GPIOA
#define BUZZER_Pin GPIO_PIN_11
#define BUZZER_GPIO_Port GPIOA
#define SWDIO_Pin GPIO_PIN_13
#define SWDIO_GPIO_Port GPIOA
#define SWCLK_Pin GPIO_PIN_14
#define SWCLK_GPIO_Port GPIOA
#define LED_B_Pin GPIO_PIN_15
#define LED_B_GPIO_Port GPIOA
#define LED_G_Pin GPIO_PIN_10
#define LED_G_GPIO_Port GPIOC
#define LED_R_Pin GPIO_PIN_11
#define LED_R_GPIO_Port GPIOC
#define REMOTE_START_Pin GPIO_PIN_12
#define REMOTE_START_GPIO_Port GPIOC
#define REMOTE_START_EXTI_IRQn EXTI15_10_IRQn
#define REMOTE_KILL_Pin GPIO_PIN_2
#define REMOTE_KILL_GPIO_Port GPIOD
#define REMOTE_KILL_EXTI_IRQn EXTI2_IRQn
#define ENC_L_B_Pin GPIO_PIN_3
#define ENC_L_B_GPIO_Port GPIOB
#define MOTOR_R_IN2_Pin GPIO_PIN_4
#define MOTOR_R_IN2_GPIO_Port GPIOB
#define MOTOR_R_IN1_Pin GPIO_PIN_5
#define MOTOR_R_IN1_GPIO_Port GPIOB
#define MOTOR_L_IN2_Pin GPIO_PIN_6
#define MOTOR_L_IN2_GPIO_Port GPIOB
#define MOTOR_L_IN1_Pin GPIO_PIN_7
#define MOTOR_L_IN1_GPIO_Port GPIOB
#define MOTOR_R_PWM_Pin GPIO_PIN_8
#define MOTOR_R_PWM_GPIO_Port GPIOB
#define MOTOR_L_PWM_Pin GPIO_PIN_9
#define MOTOR_L_PWM_GPIO_Port GPIOB

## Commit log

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2020-02-24 Created eagle project and added TC4426
    Also created a managed library.
    [robotsm20-linefollower.brd, robotsm20-linefollower.sch]
2020-02-25 Added an A3 frame in schematic
    [robotsm20-linefollower.sch]
2020-02-25 Added a bidirectional current resistor in schematic.
    Also added in shared lib.
    [robotsm20-linefollower.brd, robotsm20-linefollower.sch]
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2020-02-27 Added motor driver
    [robotsm20-linefollower.brd, robotsm20-linefollower.sch]
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2020-02-27 Added 3V3, 5V regulator
    [robotsm20-linefollower.brd, robotsm20-linefollower.sch]
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2020-02-28 Added 3V7, 1V8 regulator
    [robotsm20-linefollower.brd, robotsm20-linefollower.sch]
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2020-02-29 Completed the boost part
    [robotsm20-linefollower.brd, robotsm20-linefollower.sch]
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2020-03-03 Add MCU + MCU power to schematic + update pins in CUBEMX
    [robotsm20-linefollower.brd, robotsm20-linefollower.sch]
2020-03-05 Reset button + Boot select
    [robotsm20-linefollower.brd, robotsm20-linefollower.sch]
2020-03-05 PCB components folder for step files + button step file
    [FSM2JSMA.stp]
2020-03-05 Debug + UART connector and OLED Screen
    [robotsm20-linefollower.brd, robotsm20-linefollower.sch]
2020-03-05 Create 128x32 Oled i2c.stp
    [128x32 Oled i2c.stp]
2020-03-05 Motor driver finished except for ROSC
    [robotsm20-linefollower.brd, robotsm20-linefollower.sch]
2020-03-05 Added IMU, Battery switch, BT,
    [robotsm20-linefollower.brd, robotsm20-linefollower.sch]
2020-03-06 Added interface button
    [robotsm20-linefollower.brd, robotsm20-linefollower.sch]
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2020-03-08 Create Amass_XT30PW-M_pcb solder.stp
    [Amass_XT30PW-M_pcb solder.stp]
2020-03-08 Added rgb led, xt30 for battery and changed to nmosfet
    [robotsm20-linefollower.brd, robotsm20-linefollower.sch]
2020-03-08 Added more connectors to motors and sensor
    [robotsm20-linefollower.brd, robotsm20-linefollower.sch]
2020-03-08 Corrected some ERC
    [robotsm20-linefollower.brd, robotsm20-linefollower.sch]
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2020-03-08 Changed titles on components for easier readability.
    [robotsm20-linefollower.brd, robotsm20-linefollower.sch]
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2020-03-09 Added pulldown resistor for RGB led
    [robotsm20-linefollower.brd, robotsm20-linefollower.sch]
2020-03-09 Changed name of some parts
    [robotsm20-linefollower.brd, robotsm20-linefollower.sch]
2020-03-09 Moved groups in schematic
    [robotsm20-linefollower.sch]
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2020-03-09 Correction work
    [robotsm20-linefollower.brd, robotsm20-linefollower.sch]
2020-03-09 Checked schematic towards datasheets
    [robotsm20-linefollower.brd, robotsm20-linefollower.sch]
2020-03-09 Moved parts together for boost in board
    [robotsm20-linefollower.brd, robotsm20-linefollower.sch]
2020-03-09 Add colored pcb step models
    [BSS138L.step, FSM2JSMA.step, FSM2JSMA.stp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]
2020-03-09 Moved components in board
    [robotsm20-linefollower.brd, robotsm20-linefollower.sch]
2020-03-09 Create RGB LED Step
    [RGB-LED_15014M173100.step]
2020-03-09 3D file update on components
    [robotsm20-linefollower.brd, robotsm20-linefollower.sch]
2020-03-10 Routed motor driver, boost
    [robotsm20-linefollower.brd, robotsm20-linefollower.sch]
2020-03-10 Create JST-ZH-02 3D model
    [JST-ZH-02.step]
2020-03-10 3D packages update from components
    [robotsm20-linefollower.brd, robotsm20-linefollower.sch]
2020-03-11 Changed pinout on MCU for better layout to motor driver
    [robotsm20-linefollower.brd, robotsm20-linefollower.sch]
2020-03-11 Connect current amplifier and switch pins for Rmotor
    [robotsm20-linefollower.brd, robotsm20-linefollower.sch]
2020-03-11 Changed to DGND for all MCU components
    [robotsm20-linefollower.brd, robotsm20-linefollower.sch]
2020-03-11 Routed to motor driver
    [robotsm20-linefollower.brd, robotsm20-linefollower.sch]
2020-03-11 Routed UART and I2C
    [robotsm20-linefollower.brd, robotsm20-linefollower.sch]
2020-03-11 Change resistor and pinheader to dipswitch for RXTXBT and BOOT12
    [robotsm20-linefollower.brd, robotsm20-linefollower.sch]
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2020-03-11 Switched RL encoder pins
    [robotsm20-linefollower.brd, robotsm20-linefollower.sch]
2020-03-11 BLDC motor thrust test results
    [bldc_motor_tests.csv]
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2020-03-12 Changed testpoint to TH and rerouted due to change in design
    [robotsm20-linefollower.brd, robotsm20-linefollower.sch]
2020-03-12 Connection more airwires <3
    [robotsm20-linefollower.brd]
2020-03-12 Moved around for battery
    [robotsm20-linefollower.brd]
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2020-03-12 Added some text and Blitz V2
    [robotsm20-linefollower.brd]
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2020-03-12 Added link to github
    [robotsm20-linefollower.brd]
2020-03-12 Add/update step, decal and imgs
    [128x32 Oled i2c.stp, Amass_XT30PW-M_pcb solder.stp, BNO055.step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]
2020-03-12 Added more text and continue the DRC fun
    [robotsm20-linefollower.brd]
2020-03-13 Cleanup of BOM of unnecessary columns
    [bom.csv]
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2020-03-13 DRC and ERC check complete
    [robotsm20-linefollower.brd, robotsm20-linefollower.sch]
2020-03-13 Change some cap value to lower for C0603
    [robotsm20-linefollower.brd, robotsm20-linefollower.sch]
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2020-04-06 Switched place on silkscreen on left fan pwm
    [robotsm20-linefollower.brd, robotsm20-linefollower.sch]
2020-04-06 buzzer, motor and button setup
    [main.c, main.h, motor.c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]
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2020-04-15 Remote Arming and Disarmaring of fans
    THe SD card was replaced by the start module in order to arm and disarm the fans in case of an emergency.
    [blitz_v2.ioc, fan.c, main.c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]
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

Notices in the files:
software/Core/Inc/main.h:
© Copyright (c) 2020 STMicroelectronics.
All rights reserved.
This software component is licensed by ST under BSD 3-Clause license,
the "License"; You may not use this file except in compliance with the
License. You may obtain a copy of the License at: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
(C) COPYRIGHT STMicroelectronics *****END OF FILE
